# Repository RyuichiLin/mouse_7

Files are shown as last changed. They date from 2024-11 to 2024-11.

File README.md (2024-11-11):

# Micromouse: Mouse 7
This is a public repository for Team Kirbo's micromouse robot for IEEE of Long Island. 

This Micromouse project exists in its current state thanks to:

**Christopher Lobato**
- Implemented PID feedback loop control for the micromouse
- Troubleshooted micromouse firmware/hardware from the start of the project at Stony Brook University
- Helped transition from Arduino Nano to AT32UC3L0256 MCU using Microchip's SDK
- Troubleshooted micromouse firmware/hardware for Mouse 6 
- GOAT- countless hours of pure engineering passion and dedication

**Christopher Freeman**
- Implemented partial flood-fill algorithm from scratch starting mouse 6
- Troubleshooted micromouse firmware for Mouse 6
- GOAT- sharp, patient, and self-driven engineer

**Andy Zhuo**
- Designed a test board for alternatives to SHARP IR sensors to design a custom 3V3 IR sensor w/ similar characteristics to the SHARP sensors
- GOAT- underrated cheesecake enjoyer, can complete any task at hand

**Thomas Montchal**
- Initiated micromouse hardware design from the start of the project at Stony Brook University
- Designed 3D printed mounts for initial Mouse 4
- Helped design circuit for Mouse 4
- GOAT- competent and passionate electrical engineer, vast tinkering repertoire

**Rachel Leong**
- Implemented flood-fill algorithm for Mouse 4 at the start of the project at Stony Brook University 
- GOAT- a bright polymath and powerhouse of engineering

## Mouse 7 Active Team Members:
- Ryuichi Lin
  - Hardware design (schematic / PCB / component selection)
  - Embedded firmware development (drivers, wrappers for higher layers to utilize)
  - Initiate Python simulation effort
- Christopher Lobato
  - PID movement control development
  - Mouse movement development (acceleration/decceleration, diagonal movement via Python Simulation and w/ real hardware)
- Christopher Freeman
  - Mouse maze solving algorithm development (optimization via movement time calculation)
  - ESP32 Bluetooth serial module development (testing/verification before mouse integration)
- Andy Zhuo
  - SHARP IR sensor alternative development (schematic / PCB / component selection)
  - Command line interface development (debugging interface, data collection interface)

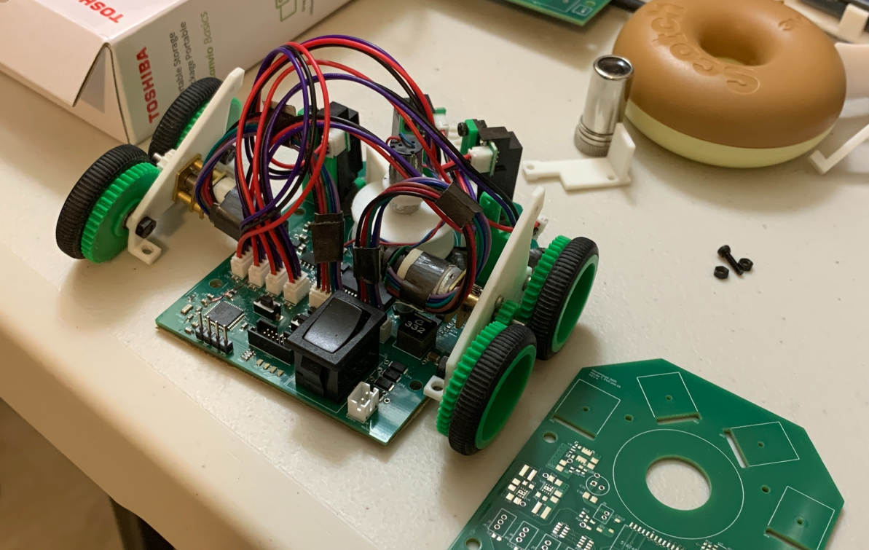
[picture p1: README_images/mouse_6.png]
Mouse 6 Image


This is the continuation of the micromouse journey- everything started in a lab with a handful of engineers and some Monster energy drinks.

## README Index
- [Repository Navigation](#repository-navigation)
- [Current Bot Overview](#current-bot-overview)
- [Work in Progress](#work-in-progress)
- [Version History](#version-history)

## Repository Navigation
- `HELP/`
  - Useful documentation for everyone:
  - Git guide
    - it's easy, and absolutely worth a quick read to use what Git provides at the bare minimum 
  - Doxygen Guide
    - important for standardizing C firmware format, and documentation generation
  - Sphinx Guide
    - important for standardizing Python software format, and documentation generation 
- `firmware/`
  - Firmware sourrce code:
    - AT32UC3L0256 MCU firmware
    - ESP32 Bluetooth module (work in progress)
- `hardware/`
  - 3D printed mount models
  - Mouse 7 hardware reference files:
    - Schematic PDF
    - PCB layout PDF
    - 3D model images
  - Bluetooth module hardware reference files:
    - Schematic PDF
    - PCB layout PDF
    - 3D model images
- `test_software/`
  - Python simulation test files

## Current Mouse Overview
- Below is a high level overview of the current micromouse and its features

### Firmware
- Mouse 7 runs on the AT32UC3L0256 MCU (32-bit AVR32 architecture MCU by Atmel/Microchip)
- Below is a block diagram outlining the firmware structure for (use Doxygen further documentation)

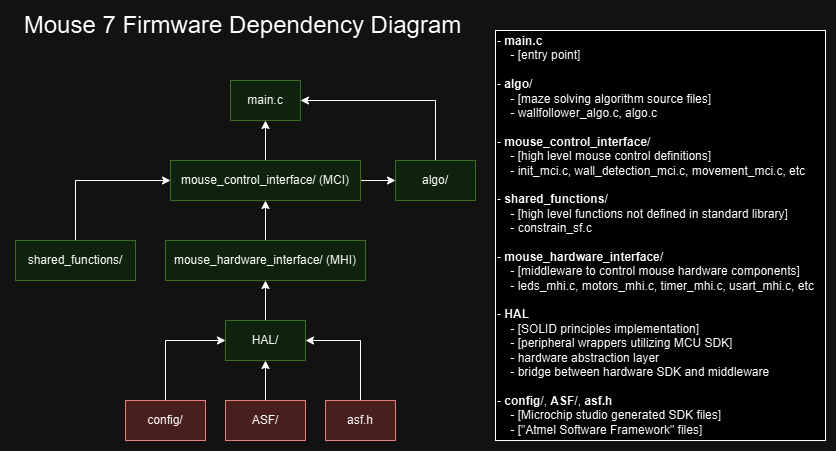
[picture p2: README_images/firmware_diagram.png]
Firmware Diagram

- Green items are written by us, red items are generated via Microchip Studio (hardware specific files)
- Mouse firmware structured to adhere to *SOLID Principles* (link: https://en.wikipedia.org/wiki/SOLID)
- Isolating hardware specific firmware under a **H**ardware **A**bstraction **L**ayer allows for easy plug and play when the time comes for a hardware upgrade or change

### Hardware
- Below is a block diagram outlining the main hardware components of Mouse 7:

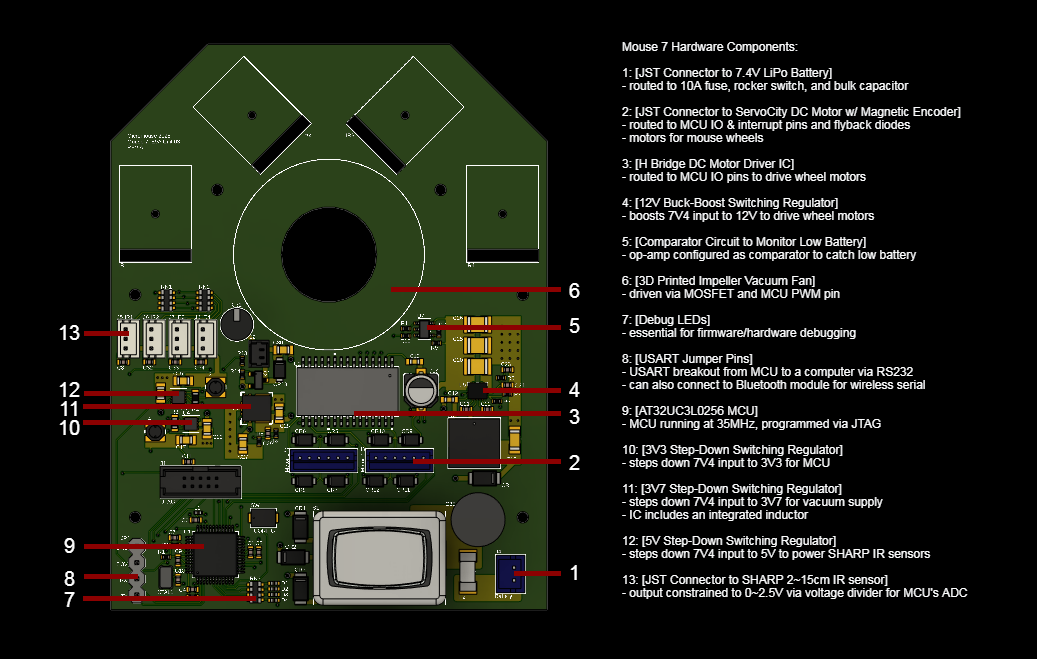
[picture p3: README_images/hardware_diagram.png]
Hardware Diagram

- Regarding the power supply circuitry, Texas Instruments has a fantastic tool to generate a circuit for whatever supply you need for your load: https://webench.ti.com/power-designer/
- Mouse 7's 3V3 and 5V circuits were found independent of the tool (Texas Instrument's regulator ICs have great documentation even without the webench tool), but the 12V and 3V7 supply circuits are webench generated, and work just fine

### Test Software
- Due to differences between the competetition maze and practice mazes, there is always a need to tune the mouse for the actual competition maze
- Python simulation software has been written to simulate hardware behavior to optimize mouse movement control and wall detection for any given maze
- Below is a block diagram outlining the test simulation structure (use Sphinx for further documentation)

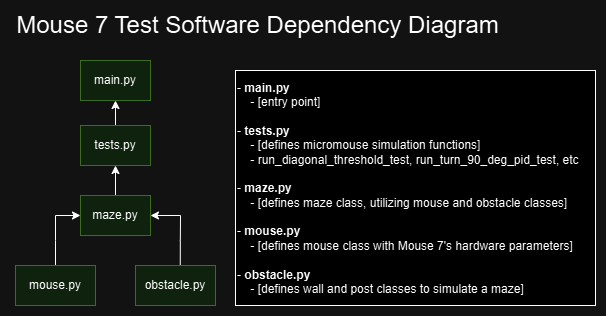
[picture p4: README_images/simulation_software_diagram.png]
Simulation Software Diagram


## Work in Progress
**Full SOLID principles implementation**
- mouse_hardware_interface layer incomplete- remove asf.h dependencies

**Python Simulation**
- simulate move forward PID (both one and two wall cases)

**Additional mouse movement options**
- diagonal movement, acceleration/decceleration, continuous movement

**Bluetooth module**
- verify functionality w/ custom made AT32UC3L0256 breakout board & Sparkfun ESP32 Bluetooth module board

**Serial command line interface**
- complete USART receive firmware for MCU 
- develop commands and appropriate responses to commands

**Maze algorithm updates**
- optimize mouse path for time taken for each type of movement (rotation, move forward, etc)

## Version History
### 1.0.0
- Initial revision
- Hardware is updated to mouse 7
- Firmware is outdated mouse 6 files
- New Python simulation files to avoid tuning mouse on the spot going forward

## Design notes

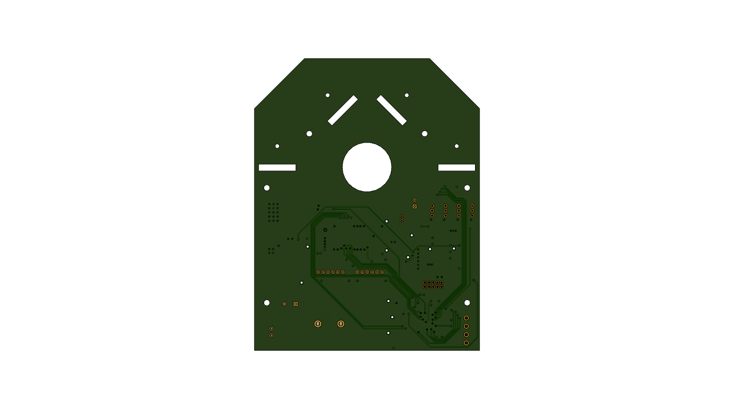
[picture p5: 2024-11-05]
hardware/mouse_7/3d_model/mouse_7_image_3.png

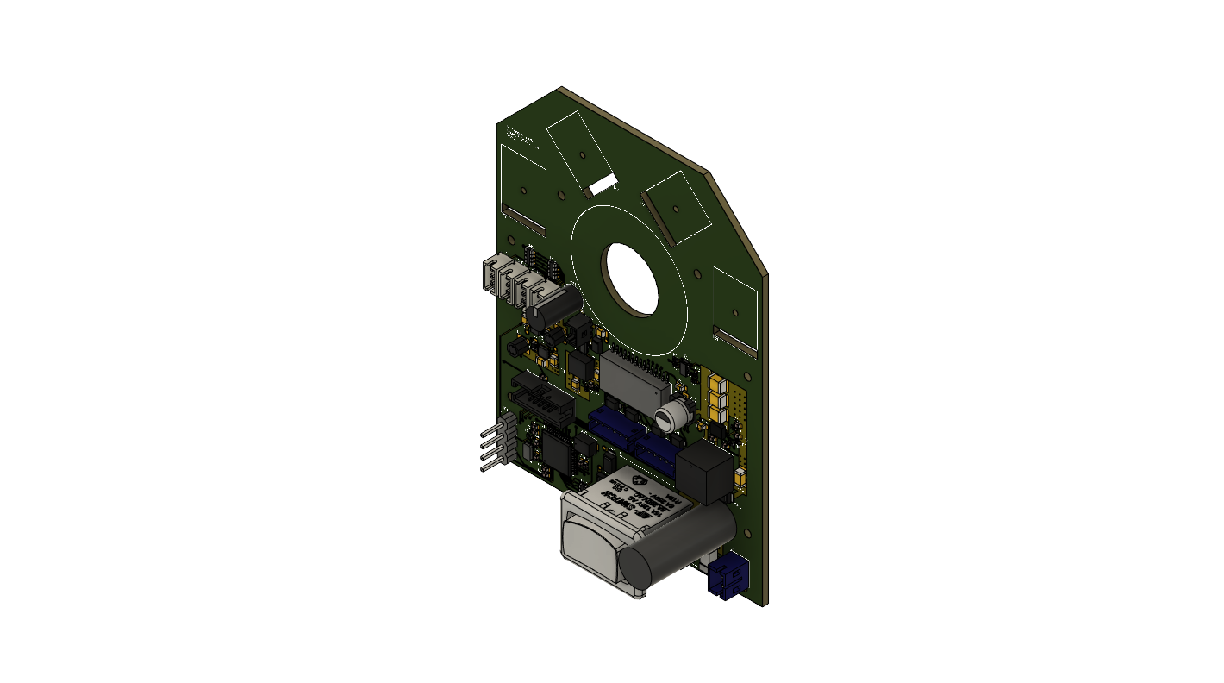
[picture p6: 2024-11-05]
hardware/mouse_7/3d_model/mouse_7_image_1.png

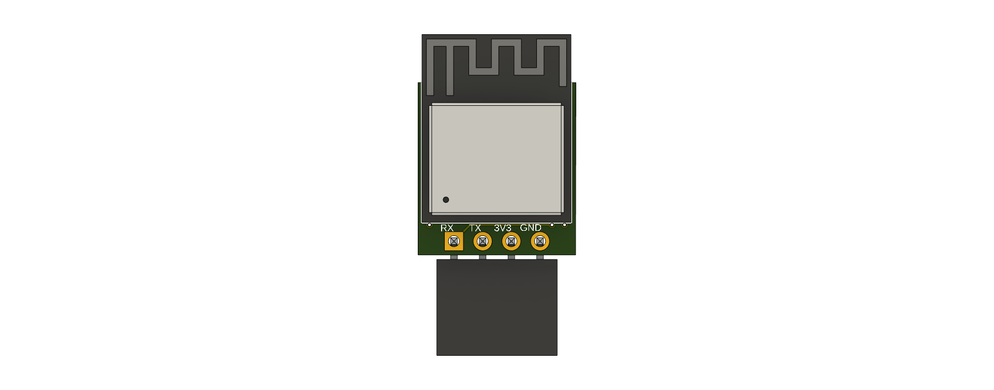
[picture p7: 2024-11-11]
hardware/bluetooth_module/3d_model/bluetooth_module_image_2.png

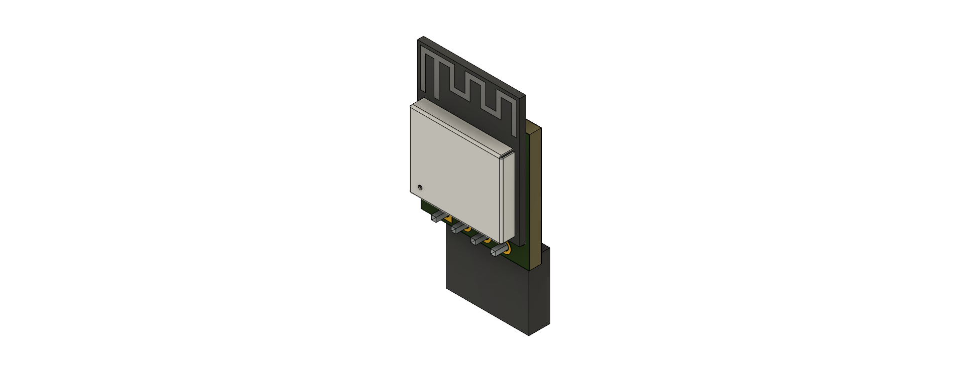
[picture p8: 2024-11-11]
hardware/bluetooth_module/3d_model/bluetooth_module_image_1.png

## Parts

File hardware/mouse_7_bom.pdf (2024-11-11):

Category | Vendor Item Number Item Description Quantity Per Package Cost Per Package Number of Packages Item Total Cost Part Link Symbol, Layout, & Designation on Mouse 7.0 Test Designation on Mouse 7.0 PCB 3D Model Link Comments
| - 7.4V LiPo battery, 900mAh, 46g, 30C - JST PH 2.0 pitch 2 position for power, 3 position for charging - 53mm x 16mm x 29mm (l x h x w)
| - JST PH 2.0 pitch 2 position pack both male and female TH - 50 male, 50 female

Power

Amazon | B096G4D6ZX URGENEX 7.4V Lipo Battery 2S 30C 900mAh Rechargeable Lipo Battery with PH2.0 Plug Compatible with Most 1/10, 1/16, 1/18, 1/24 Scale RC Cars Trucks 2 | $19.99 | 1 | $19.99 https://www.amazon.com/URGENEX-Battery-900mAh-Rechargeable-Campatibal/dp/B096G4D6ZX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
Amazon | B09DP9FZTX | CQRobot 50 Sets/200 Pieces 2.0 mm Pitch JST PH 2-Pin IC Sockets & Plugs Adapter Connector Male and Female Terminal, Crimp DIP Kit. for Industrial Integrated Circuit JST Connector Cable. 50 | $7.99 | 1 | $7.99 https://www.amazon.com/CQRobot-Connector-Terminal-Industrial-Integrated/dp/B09DP9FZTX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
Digikey | CMS04(TE12LQM)CT-ND DIODE SCHOTTKY 30V 5A M-FLAT 1 | $0.76 | 4 | $3.04 https://www.digikey.com/en/products/detail/toshiba-semiconductor-and-storage/CMS04-TE12L-Q-M/871534 https://app.ultralibrarian.com/details/873d4c59-1bbb-11ea-a124-0ad2c9526b44/Toshiba-Electronic-Devices-Storage-Corp-/CMS04-TE12L-Q-M-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
- schottky diode for everything except vacuum that needs 5A
- prevents up to 30V and allows 5A to pass
- for 3.3V, 5V, 12V, and 3.2V regulators
- small 370mV forward drop
Digikey | 296-53563-1-ND DC DC CONVERTER 1.2-6V | 1 | $3.48 | 1 | $3.48 https://www.digikey.com/en/products/detail/texas-instruments/TPSM84209RKHR/10273205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 https://app.ultralibrarian.com/details/72767a0a-9a13-11e9-ab3a-0a3560a4cccc/Texas-Instruments/TPSM84209RKHR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
- 3.7V 2A regulator for vacuum motor
- schematic generated w/ TI tool: HERE HERE
Digikey | 445-7665-1-ND CAP CER 22UF 10V X5R 0805 1 | $0.39 | 2 | $0.78 https://www.digikey.com/en/products/detail/tdk-corporation/C2012X5R1A226M125AB/2733100 n/a
- Cin for vacuum fan regulator circuit
- 0805 package
- 22uF
Digikey | 445-8239-1-ND CAP CER 47UF 10V X5R 0805 1 | $0.79 | 3 | $2.37 https://www.digikey.com/en/products/detail/tdk-corporation/C2012X5R1A476M125AC/2812455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 n/a
- Cout for vacuum fan regulator circuit
- 0805 package
- 47uF
Digikey | 399-C0402C331J5JAC7867CT-ND CAP CER 330PF 50V U2J 0402 1 | $0.24 | 1 | $0.24 https://www.digikey.com/en/products/detail/kemet/C0402C331J5JAC7867/6176500 n/a
- Cff for vacuum fan regulator circuit
- 0402 package
- 330pF
Digikey | 541-10.0KLCT-NDRES SMD 10K OHM 1% 1/16W 0402 1 | $0.10 | 1 | $0.10 https://www.digikey.com/en/products/detail/vishay-dale/CRCW040210K0FKED/1178121 n/a
- Rfbt for vacuum fan regulator circuit
- 0402 package
- 10k Ohm resistor
Digikey | 541-1.91KLCT-NDRES SMD 1.91K OHM 1% 1/16W 0402 1 | $0.10 | 1 | $0.10 https://www.digikey.com/en/products/detail/vishay-dale/CRCW04021K91FKED/1178037 n/a
- Rfbb for vacuum fan regulator circuit
- 0402 package
- 1.91k Ohm resistor
Digikey | 296-TPS61288RQQRCT-ND IC REG BOOST ADJ 15A 11VQFN1 | $5.89 | 1 | $5.89 https://www.digikey.com/en/products/detail/texas-instruments/TPS61288RQQR/13627146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 https://app.ultralibrarian.com/details/b8fe61ee-f9ad-11ea-b55a-0a34d6323d74/Texas-Instruments/TPS61288RQQR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
- 12V 3A regulator for wheel motor driver
- schematic generated w/ TI tool: https://webench.ti.com/appinfo/webench/scripts/SDP.cgi?ID=AA12043C39DD7B4B
Digikey | 445-4042-1-ND CAP CER 10UF 16V X7R 1206 1 | $0.30 | 1 | $0.30 https://www.digikey.com/en/products/detail/tdk-corporation/C3216X7R1C106K160AC/1965630 n/a
- Cin for wheel motor regulator circuit
- 1206 package
- 10uF
Digikey | 445-1314-1-ND CAP CER 0.1UF 50V X7R 0603 1 | $0.10 | 1 | $0.10 https://www.digikey.com/en/products/detail/tdk-corporation/C1608X7R1H104K080AA/513811 n/a
- Cinx for wheel motor regulator circuit
- 0603 package
- 0.1uF
Coilcraft | XAL7070-332 | XAL7070-332MEC | 1 | $3.25 | 1 | $3.25 https://www.coilcraft.com/en-us/products/power/shielded-inductors/molded-inductor/xal/xal7070/xal7070-332/ https://app.ultralibrarian.com/details/c70f84e9-0c17-11ee-9288-0ae0a3b49db5/Coilcraft/XAL7070-332MEC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 - L1 for wheel motor regulator circuit
Digikey | 445-4952-1-ND CAP CER 0.1UF 16V X7R 0402 1 | $0.10 | 1 | $0.10 https://www.digikey.com/en/products/detail/tdk-corporation/C1005X7R1C104K050BC/2093220 n/a
- Cbst for wheel motor regulator circuit
- 0402 package
- 0.1uF
Digikey | 445-9097-1-ND CAP CER 2.2UF 10V X7S 0402 1 | $0.29 | 1 | $0.29 https://www.digikey.com/en/products/detail/tdk-corporation/C1005X7S1A225K050BC/3661557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 n/a
- Cvcc for wheel motor regulator circuit
- 0402 package
- 2.2uF
Digikey | 541-34.0KLCT-NDRES SMD 34K OHM 1% 1/16W 0402 1 | $0.10 | 1 | $0.10 https://www.digikey.com/en/products/detail/vishay-dale/CRCW040234K0FKED/1178180 n/a
- Rcomp for wheel motor regulator circuit
- 0402 package
- 34k Ohms
Digikey | 490-16432-1-ND CAP CER 0.039UF 16V X7R 04021 | $0.10 | 1 | $0.10 https://www.digikey.com/en/products/detail/murata-electronics/GCM155R71C393KA37D/7363176 n/a
- Ccomp for wheel motor regulator circuit
- 0402 package
- 39nF
Digikey | 399-11256-1-ND CAP CER 82PF 25V C0G/NP0 0402 1 | $0.49 | 1 | $0.49 https://www.digikey.com/en/products/detail/kemet/CBR04C820F3GAC/4377017 n/a
- Ccomp2 for wheel motor regulator circuit
- 0402 package
- 82pF
Digikey | 541-931KLCT-NDRES SMD 931K OHM 1% 1/16W 0402 1 | $0.10 | 1 | $0.10 https://www.digikey.com/en/products/detail/vishay-dale/CRCW0402931KFKED/1178346 n/a
- Rfbt for wheel motor regulator circuit
- 0402 package
- 931k Ohms
Digikey | 541-48.7KLCT-NDRES SMD 48.7K OHM 1% 1/16W 0402 1 | $0.10 | 1 | $0.10 https://www.digikey.com/en/products/detail/vishay-dale/CRCW040248K7FKED/1178199 n/a
- Rfbb for wheel motor regulator circuit
- 0402 package
- 48.7k Ohms
Digikey | 490-16309-1-ND CAP CER 47UF 16V X6S 1210 1 | $0.52 | 3 | $1.56 https://www.digikey.com/en/products/detail/murata-electronics/GRM32EC81C476KE15K/7363053 n/a
- Cout for wheel motor regulator circuit
- 1210 package
- 47uF
Digikey | EG5554-ND | SWITCH ROCKER SPST 15A 125V 1 | $1.64 | 1 | $1.64 https://www.digikey.com/en/products/detail/e-switch/R1966ABLKBLKEP/1805067 - https://www.mouser.com/ProductDetail/E-Switch/R1966ABLKBLKEP?qs=fwxlpxwtDRcZsx8M4AZ8tA%3D%3D
- switch for on/off of entire mouse
- rated for 15A (AC), can hopefully handle 9A DC
Digikey | 283-5179-1-ND FUSE BRD MNT 10A 125VAC/VDC 2SMD 1 | $0.91 | 1 | $0.91 https://www.digikey.com/en/products/detail/eaton-electronics-division/CB61F10A-TR2/3526138 https://www.mouser.com/ProductDetail/Bussmann-Eaton/CB61F10A-TR2?qs=3W28jC%252BmlM2sYw8RFxQ%2Faw%3D%3D
- 10A fuse for entire mouse
- 3A for wheels + 2A for vacuum + 1A for 3.3V + 1A for 5V = 7A | Extra new
Digikey | P122314CT-ND CAP ALUM 1200UF 20% 16V RADIAL 1 | $0.49 | 1 | $0.49 https://www.digikey.com/en/products/detail/panasonic-electronic-components/EEU-FS1C122LB/7381180 https://www.mouser.com/ProductDetail/Panasonic/EEU-FS1C122LB?qs=gt1LBUVyoHmQ1%252BC95E8BAw%3D%3D - 1.2mF 16V bulk cap for entire mouse | Extra new
Digikey | 296-39450-1-ND IC REG BUCK 5V 500MA 8WSON1 | $1.36 | 1 | $1.36 https://www.digikey.com/en/products/detail/texas-instruments/TPS62173DSGR/2833458 https://app.ultralibrarian.com/details/16ac426d-103f-11e9-ab3a-0a3560a4cccc/Texas-Instruments/TPS62173DSGR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
- 5V, 500mA switching regulator
- used to power Sharp sensors
Digikey | 296-39449-1-ND IC REG BUCK 3.3V 500MA 8WSON 1 | $1.36 | 1 | $1.36 https://www.digikey.com/en/products/detail/texas-instruments/TPS62172DSGR/2833456 https://app.ultralibrarian.com/details/16ac3ea9-103f-11e9-ab3a-0a3560a4cccc/Texas-Instruments/TPS62172DSGR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
- 3.3V, 500mA switching regulator
- used to power MCU
Digikey | 445-6857-1-ND CAP CER 10UF 10V X7R 0805 1 | $0.31 | 2 | $0.62 https://www.digikey.com/en/products/detail/tdk-corporation/C2012X7R1A106K125AC/2619198 n/a
- 10uF ceramic cap needed for 5V and 3.3V switching regulator
- between VIN and PGND (pg 21 pdf of datasheet)
- 0805 package

Category | Vendor | Item Number

Item Description

Quantity Per Package

Cost Per Package

Number of Packages | Item Total Cost | Part Link

Symbol, Layout, &
3D Model Link | Comments

Designation on Mouse 7.0 Test

Designation on Mouse 7.0 PCB

Digikey | 445-7665-1-ND CAP CER 22UF 10V X5R 0805 1 | $0.39 | 2 | $0.78 https://www.digikey.com/en/products/detail/tdk-corporation/C2012X5R1A226M125AB/2733100 n/a
- 22uF ceramic cap needed for 5V and 3.3V switching regulator
- between SW and FB (pg 21 pdf of datasheet)
Digikey | 541-100KHCT-NDRES SMD 100K OHM 1% 1/10W 0603 1 | $0.10 | 2 | $0.20 https://www.digikey.com/en/products/detail/vishay-dale/CRCW0603100KFKEA/1174896 n/a
- 100k Ohm resistor needed for 5V and 3.3V switching regulator
- between SW/VOS and PG (pg 21 pdf of datasheet)
- smaller 0603 package
Digikey | 732-2613-1-ND FIXED IND 2.2UH 1.8A 66 MOHM SMD 1 | $1.64 | 2 | $3.28 https://www.digikey.com/en/products/detail/w%C3%BCrth-elektronik/744025002/2445620 https://www.mouser.com/ProductDetail/Wurth-Elektronik/744025002?qs=rS3zZhy2AQOJdJOD4WhGug%3D%3D
- 2.2uH inductor needed for 5V and 3.3V switching regulator
- between SW and 100k Ohm resistor (pg 21 pdf of datasheet) | (NEW, old dupe)
Digikey | 296-TLV9301IDBVRCT-ND IC OPAMP GP 1 CIRCUIT SOT23-5 1 | $0.58 | 1 | $0.58 https://www.digikey.com/en/products/detail/texas-instruments/TLV9301IDBVR/12165123 https://app.ultralibrarian.com/details/268976cb-c80b-11e9-ab3a-0a3560a4cccc/Texas-Instruments/TLV9301IDBVR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
- low battery voltage indicator op amp
- to be used as comparator to turn on/off regulators
Digikey | P118KLCT-ND | RES SMD 118K OHM 1% 1/10W 0402 1 | $0.10 | 1 | $0.10 https://www.digikey.com/en/products/detail/panasonic-electronic-components/ERJ-2RKF1183X/192103 n/a
- R2 for low battery voltage comparator circuit
- 0402 package
- 118k Ohms
Digikey | 541-100KLCT-NDRES SMD 100K OHM 1% 1/16W 0402 1 | $0.10 | 1 | $0.10 https://www.digikey.com/en/products/detail/vishay-dale/CRCW0402100KFKED/1178235 n/a
- R1 for low battery voltage comparator circuit
- 0402 package
- 100k Ohms
Digikey | 541-10.0KLCT-NDRES SMD 10K OHM 1% 1/16W 0402 1 | $0.10 | 1 | $0.10 https://www.digikey.com/en/products/detail/vishay-dale/CRCW040210K0FKED/1178121 n/a
- R1 for comparator output divider
- 0402 package
- 10k ohms | (NEW, dupe)
Digikey | P3.74KLCT-ND RES SMD 3.74K OHM 1% 1/10W 0402 1 | $0.10 | 1 | $0.10 https://www.digikey.com/en/products/detail/panasonic-electronic-components/ERJ-2RKF3741X/192286 n/a
- R2 for comparator output divider
- 0402 package
- 3.74k ohms | NEW

Wheel Motor Related

Digikey | TB6561FG8ELCT-ND IC MOTOR DRIVER 10V-36V 30SSOP 1 | $3.51 | 1 | $3.51 https://www.digikey.com/en/products/detail/toshiba-semiconductor-and-storage/TB6561FG-8-EL/1730056 https://app.ultralibrarian.com/details/84a3ee1c-5a2c-11eb-9033-0a34d6323d74/Toshiba-Electronic-Devices-Storage-Corp-/TB6561FG-8-EL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
- H bridge PWM interface brushed motor driver
- 10-36V supply, 3A output max, 30-BSOP
Digikey | 445-7456-1-ND CAP CER 0.1UF 50V X5R 0603 1 | $0.11 | 1 | $0.11 https://www.digikey.com/en/products/detail/tdk-corporation/C1608X5R1H104K080AA/2732891 n/a
- C2 0.1uF cap for 5V output from motor driver
- datasheet pg 8: HERE
- 0603 package
Digikey | P121394CT-ND CAP ALUM HYB 47UF 20% 25V SMD 1 | $1.45 | 1 | $1.45 https://www.digikey.com/en/products/detail/panasonic-electronic-components/EEH-ZK1E470R/6564642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 https://www.mouser.com/ProductDetail/Panasonic/EEH-ZK1E470R?qs=FNcb6ahWXRxnLCe3Ulph5A%3D%3D
- C1 47uF polymer cap for motor driver supply
- datasheet pg 8
Servocity | 638103 Gear Motor with Encoder | 1 | $19.99 | 2 | $39.98 https://www.servocity.com/4900-rpm-micro-gear-motor-w-encoder/
- Gear motors, 4900rpm w/ encoders
- 6 position 1.5 pitch ZH JST
Pololu | 1087 Black plastic wheels with silicone tires 2 | $4.95 | 1 | $4.95 https://www.pololu.com/product/1087
- Wheels, 32mm diameter, 3mm D output shaft
- we'll use just the rubber tire and make a custom wheel
Amazon | B09NCCXPGM CQRobot 100 Sets/800 Pieces 1.5 mm Pitch JST ZH 6-Pin IC Sockets & Plugs Adapter Connector Male and Female Terminal, Crimp DIP Kit. for Industrial Integrated Circuit JST Connector Cable. 100 | $9.58 | 1 | $9.58 https://www.amazon.com/CQRobot-Connector-Terminal-Industrial-Integrated/dp/B09NCCXPGM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

https://www.jst-mfg.com/product/index.php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 - JST ZH 6 position male (receptacle) TH connector
Amazon | B07FW18RQY | uxcell 683ZZ Ball Bearing 3mm x 7mm x 3mm Double Shielded Deep Groove Bearings, Carbon Steel 20pcs 20 | $7.99 | 1 | $7.99 https://www.amazon.com/uxcell-Bearing-Double-Shielded-Bearings/dp/B07FW18RQY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 - 3mm ball bearings to be embedde into custom wheels
Servocity | 1500-0010-0003 1500 Series Plastic Spacer (3mm ID x 5mm OD, 1mm Thickness) - 12 Pack 12 | $1.87 | 1 | $1.87 https://www.servocity.com/1500-series-plastic-spacer-3mm-id-x-5mm-od-1mm-thickness-12-pack/ - 3mm plastic spacers to put between wheel and mount
Amazon | B0BKRQSMFL FOLIV 700PCS M3 x 5/6/8/10/12/14/16/18/20/25/30mm Button Hex Head Cap Screws M3 Metric Machine Screws Bolts Nuts Washer Assortment Kit, 10.9 Grade Alloy Steel 10-50 | $15.29 | 1 | $15.29 https://www.amazon.com/gp/product/B0BKRQSMFL/ref=ox_sc_act_title_1?smid=A3ILXS83DKRO8O&th=1 - M3 button head screws to serve as wheel axels
Digikey | 1727-7806-1-ND DIODE SCHOTTKY 60V 3A SOD123W 1 | $0.39 | 8 | $3.12 https://www.digikey.com/en/products/detail/nexperia-usa-inc/PMEG60T30ELRX/9086223 https://app.ultralibrarian.com/details/785255d6-6dbf-11ee-9288-0ae0a3b49db5/Nexperia/PMEG60T30ELRX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 - Flyback diodes for EMF protection

Vacuum Fan Related

Amazon | B08RMQP6YP 1.25mm Male and Female Connectors Socket and Plug with Pre-Crimped Cables Compatible with JST Molex PicoBlade 1.25 for Pixhawk Silicone 13cm Wire (Male and Female) 20 | $18.99 | 1 | $18.99 https://www.amazon.com/Connectors-Pre-Crimped-Compatible-PicoBlade-Silicone/dp/B08RMQP6YP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 n/a
- Molex picoblade connector various positions,
- includes 3 position 1.25mm pitch male and female connector, 20 of each
- includes 10cm precrimped wire
- to be used to extend HGLRC wire
Digikey | DMN3200U-7DICT-ND MOSFET N-CH 30V 2.2A SOT23-31 | $0.45 | 1 | $0.45 https://www.digikey.com/en/products/detail/diodes-incorporated/DMN3200U-7/1778821 https://www.mouser.com/ProductDetail/Diodes-Incorporated/DMN3200U-7?qs=oDfC%252BbpzniwrIf3%2FMV01IQ%3D%3D - 2.2A 30V MOSFET to switch on/off regulator power to vacuum fan | NEW
Digikey | P17216CT-ND | RES 47 OHM 1% 1/4W 0402 | 1 | $0.23 | 1 | $0.23 https://www.digikey.com/en/products/detail/panasonic-electronic-components/ERJ-PA2F47R0X/5402642 n/a | - 47 Ohm gate resistor for MOSFET to limit surge curernt | NEW
Digikey | 541-10.0KLCT-NDRES SMD 10K OHM 1% 1/16W 0402 1 | $0.10 | 1 | $0.10 https://www.digikey.com/en/products/detail/vishay-dale/CRCW040210K0FKED/1178121 n/a
- 10k Ohm resistor for pulling down input to MOSFET to ensure low
| | | | | | | - 0402 package | (NEW, dupe)
Digikey | 493-3813-1-ND RNE1C101MDS1PX | 1 | $0.76 | 1 | $0.76 https://www.digikey.com/en/products/detail/nichicon/RNE1C101MDS1PX/2239221 https://app.ultralibrarian.com/details/8611d1e7-1076-11e9-ab3a-0a3560a4cccc/Nichicon/RNE1C101MDS1PX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 100uF capacitor for vacuum fan driver
Digikey | 4988-NMC0805X7R104K50TRPFCT-ND CAP SMT08050.1F50VDC | 1 | $0.24 | 1 | $0.24 https://www.digikey.com/en/products/detail/nic-components-corp/NMC0805X7R104K50TRPF/18895932 n/a
- 0.1uF cap for brushless motor driver
- 0805 package
Amazon | B07CFQMF1M 8pcs 8520 Motor 8.5x20mm 15000KV Brushed Motors 4CW 4CCW Coreless Motor with JST-1.25 Connector for D JI Ryze Tello 720P Camera WiFi FPV RC Quadcopter M80S E013 Plus Tiny 8X Frame Kit etc 8 | $18.99 | 1 | $18.99 https://www.amazon.com/8-5x20mm-15000KV-Coreless-JST-1-25-Connector/dp/B07CFQMF1M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 n/a
- 15000KV brushed DC motor for vacuum fan
- 2p 1.25mm pitch picoblade connector
Digikey | WM1731-ND | CONN HEADER VERT 2POS 1.25MM 1 | $0.23 | 1 | $0.23 https://www.digikey.com/en/products/detail/molex/0530470210/242853?s=N4IgTCBcDaIKwGYAMAWA7EsBGJIC6AvkA
- https://app.ultralibrarian.com/details/56453440-d29f-11ea-b5d0-0aebb021a1ea/Molex-Connector-Corporation/530470210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
- https://www.molex.com/en-us/products/part-detail/530470210
- motor to board connector for vacuum fan
- 2p 1.25mm pitch picoblade connector
Digikey | 1727-7806-1-ND DIODE SCHOTTKY 60V 3A SOD123W 1 | $0.39 | 2 | $0.78 https://www.digikey.com/en/products/detail/nexperia-usa-inc/PMEG60T30ELRX/9086223 https://app.ultralibrarian.com/details/785255d6-6dbf-11ee-9288-0ae0a3b49db5/Nexperia/PMEG60T30ELRX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 - Flyback diodes for EMF protection

Ball Caster,
nuts, screws
Amazon | B0BTYDZVM8 | 1 Oz (23 Grams) 3000-CPS Super Glue All Purpose with Anti Clog Cap. Ca Glue - Adhesive SuperGlue. Cyanoacrylate Glue for Hard Plastics, DIY Craft, Metal and Many More 1 | $6.99 | 1 | $6.99 https://www.amazon.com/gp/product/B0BTYDZVM8/ref=sw_img_1?smid=A3O523LQQ2NT7Z&th=1 - superglue to attach 3D printed mounts to PCB

Category | Vendor | Item Number

Item Description

Quantity Per Package

Cost Per Package

Number of Packages | Item Total Cost | Part Link

Symbol, Layout, &
3D Model Link | Comments

Designation on Mouse 7.0 Test

Designation on Mouse 7.0 PCB

IR Sensing

Digikey | 1855-1027-ND | SENSOR OPTICAL 2-15CM ANALOG 1 | $8.45 | 4 | $33.80 https://www.digikey.com/en/products/detail/sharp-socle-technology/GP2Y0A51SK0F/4103863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 https://www.mouser.com/ProductDetail/Sharp-Microelectronics/GP2Y0A51SK0F?qs=Qrpqs4v%252BmsahSKJyPt06pw%3D%3D
- Sharp IR distance sensor 2-15cm
- shortest range sharp IR sensor available
- connects w/ 3 position ZH JST connector
- needs 10uF cap
Amazon | B09NC8Y2PK | CQRobot 100 Sets/500 Pieces 1.5 mm Pitch JST ZH 3-Pin IC Sockets & Plugs Adapter Connector Male and Female Terminal, Crimp DIP Kit. for Industrial Integrated Circuit JST Connector Cable. 50 | $11.99 | 1 | $11.99 https://www.amazon.com/CQRobot-Connector-Terminal-Industrial-Integrated/dp/B09NC8Y2PK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 https://www.jst-mfg.com/product/index.php?series=290
- JST ZH 1.5 pitch 3 position pack both male and female TH
- 50 male, 50 female
Digikey | 490-GRM155R61A106ME11DCT-ND CAP CER 10UF 10V X5R 0402 1 | $0.13 | 4 | $0.52 https://www.digikey.com/en/products/detail/murata-electronics/GRM155R61A106ME11D/12091056 n/a
- 10uF ceramic capacitor, SMD 0402
- needed for Sharp IR sensors | NEW
Digikey | CAY16-1001F4LFCT-ND RES ARRAY 4 RES 1K OHM 12061 | $0.10 | 1 | $0.10 https://www.digikey.com/en/products/detail/bourns-inc/CAY16-1001F4LF/2566504 https://app.ultralibrarian.com/details/ccdadb33-1071-11e9-ab3a-0a3560a4cccc/Bourns-Electronics/CAY16-1001F4LF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
- R1 resistor array to drop 2.5V max from IR sensor output to 1.8V
- 1k Ohm resistor array, 4 resistors
Digikey | CAY16-2201F4LFCT-ND RES ARRAY 4 RES 2.2K OHM 1206 1 | $0.10 | 1 | $0.10 https://www.digikey.com/en/products/detail/bourns-inc/CAY16-2201F4LF/2566534 https://app.ultralibrarian.com/details/1c159e3e-f9f4-11ed-b159-0a34d6323d74/Bourns-Electronics/CAY16-2201F4LF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
- R2 resistor to drop 2.5V max from IR sensor output to 1.8V
- 2.2k Ohms calculated w/ voltage divider equation
- resistor array, 4 resistors

MCU

Digikey | 1175-1733-ND | CONN HEADER VERT 10POS 1.27MM 1 | $0.68 | 1 | $0.68 https://www.digikey.com/en/products/detail/cnc-tech/3221-10-0100-00/4878932 https://www.arrow.com/en/products/3221-10-0100-00/cnc-tech-llc
- 2x5 TH JTAG programming header
- small 1.27 pitch w/ key slot and shroud
Digikey | 2151-RT3215-32.768-12.5-TR-10PPMCT-ND CRYSTAL 32.7680KHZ 12.5PF SMD 1 | $0.42 | 1 | $0.42 https://www.digikey.com/en/products/detail/raltron-electronics/RT3215-32-768-12-5-TR-10PPM/13151073 https://app.ultralibrarian.com/details/ce5d9187-838b-11ec-9033-0a34d6323d74/Raltron/RT3215-32-768-12-5-TR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 - 32.768kHz external crystal
Digikey | 490-GQM1555C2D220FB01DCT-ND CAP CER 22PF 200V NP0 04021 | $0.61 | 2 | $1.22 https://www.digikey.com/en/products/detail/murata-electronics/GQM1555C2D220FB01D/5882005 https://app.ultralibrarian.com/details/d28e9410-f5b2-11eb-9033-0a34d6323d74/Murata/GQM1555C2D3R5CB01J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
- 22pF caps for external crystal
- needed on each crystal terminal
- 0402 package | NEW
Amazon | B07BJJC3R6 | NOYITO TTL to RS232 Module TTL RS232 Male Female Mutual Conversion Module Serial Level Conversion to SP232 TTL Serial Port Communicates with RS232 Level Device 15KV ESD Protect (Female) 1 | $7.99 | 1 | $7.99 https://www.amazon.com/NOYITO-Module-Conversion-Arduino-communicates/dp/B07BJJC3R6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 not needed | - TTL to DB-9 (DE-9) translator for serial out
Amazon | B0759HSLP1 | OIKWAN USB to RS232, USB Serial Adapter with FTDI Chipset,USB 2.0 to Male DB9 Serial Cable for Windows 11,10, 8, 7, Vista, XP, 2000, Linux and Mac OS(6ft)… 1 | $11.99 | 1 | $11.99 https://www.amazon.com/Adapter-Chipset%EF%BC%8CDB9-Serial-Converter-Windows/dp/B0759HSLP1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 not needed | - DB-9 (DE-9) to USB A for serial out
Digikey | AT32UC3L0256-AUT-ND IC MCU 32BIT 256KB FLASH 48TQFP 1 | $10.19 | 1 | $10.19 https://www.digikey.com/en/products/detail/microchip-technology/AT32UC3L0256-AUT/3046397 https://app.ultralibrarian.com/details/89115949-109b-11e9-ab3a-0a3560a4cccc/Microchip/AT32UC3L0256-AUT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
- AT32UC3L0256 AVR MCU to replace Arduino
- 50MHz, faster than controller above, operates on 3.3V
- 12b ADC, PWM, programmed via JTAG and aWire
- schematic checklist: HERE
Digikey | 490-GRM155R61A106ME11DCT-ND CAP CER 10UF 10V X5R 0402 1 | $0.13 | 1 | $0.13 https://www.digikey.com/en/products/detail/murata-electronics/GRM155R61A106ME11D/12091056 n/a
- 10uF capacitor for AT32UC3L0256 VDDin
- page 4 of schematic checklist
- small 0402 package | NEW
Digikey | 445-4952-1-ND CAP CER 0.1UF 16V X7R 0402 1 | $0.10 | 3 | $0.30 https://www.digikey.com/en/products/detail/tdk-corporation/C1005X7R1C104K050BC/2093220 n/a
- 0.1uf ceramic cap for AT32UC3L0256 VDDin, VDDio, and VDDcore
- page 4 of schematic checklist
- 0402 package | (NEW, dupe)
Digikey | 445-9097-1-ND CAP CER 2.2UF 10V X7S 0402 1 | $0.29 | 1 | $0.29 https://www.digikey.com/en/products/detail/tdk-corporation/C1005X7S1A225K050BC/3661557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 n/a
- 2.2uF ceramic cap for AT32UC3L0256 VDDio, and VDDcore
- page 4 of schematic checklist
- 0402 package | (NEW, dupe)
Digikey | 445-4952-1-ND CAP CER 0.1UF 16V X7R 0402 1 | $0.10 | 1 | $0.10 https://www.digikey.com/en/products/detail/tdk-corporation/C1005X7R1C104K050BC/2093220 n/a
- 0.1uF ceramic cap for AT32UC3L0256 VDDana and ADVREF
- page 5 of schematic checklist
- 0402 package | (NEW, dupe)
Digikey | 732-74269241152CT-ND WETMSB SMT EMI SUPPRESSION FERR 1 | $0.13 | 1 | $0.13 https://www.digikey.com/en/products/detail/w%C3%BCrth-elektronik/74269241152/17830009 https://app.ultralibrarian.com/details/ab67cd4b-c364-11ed-b159-0a34d6323d74/Wurth-Electronics/74269244182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
- ferrite bead for for AT32UC3L0256 VDDana and ADVREF
- page 5 of schematic checklist, and page 15 on xplained dev board schematic: HERE
- 0402 package | NEW
Digikey | 445-4952-1-ND CAP CER 0.1UF 16V X7R 0402 1 | $0.10 | 1 | $0.10 https://www.digikey.com/en/products/detail/tdk-corporation/C1005X7R1C104K050BC/2093220 n/a
- 0.1uF ceramic cap for JTAG on AT32UC3L0256
- 0402 package | (NEW, dupe)
Digikey | 541-10.0KLCT-NDRES SMD 10K OHM 1% 1/16W 0402 1 | $0.10 | 1 | $0.10 https://www.digikey.com/en/products/detail/vishay-dale/CRCW040210K0FKED/1178121 n/a
- 10k resistor for pulling down enable signal
- 0402 package | (NEW, dupe)

Bluetooth

Digikey | 1965-ESP32-PICO-MINI-02-N8R2CT-ND RF TXRX MOD BT WIFI THCHAS MNT 1 | $3.50 | 1 | $3.50 https://www.digikey.com/en/products/detail/espressif-systems/ESP32-PICO-MINI-02-N8R2/14317715

https://www.mouser.com/ProductDetail/Espressif-Systems/ESP32-PICO-MINI-02-N8R2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

- ESP32 bluetooth module to serve as a serial bridge between mouse and laptop
- perfect for our application- Sparkfun has a dev board doing exactly what we want | Extra Extra new
Digikey | 445-9077-1-ND CAP CER 22UF 10V X5R 0603 1 | $0.34 | 1 | $0.34 https://www.digikey.com/en/products/detail/tdk-corporation/C1608X5R1A226M080AC/3661560 n/a
- 22uF cap to decouple ESP32 module power
- 0603 package | Extra Extra new
Digikey | 445-4952-1-ND CAP CER 0.1UF 16V X7R 0402 1 | $0.10 | 1 | $0.10 https://www.digikey.com/en/products/detail/tdk-corporation/C1005X7R1C104K050BC/2093220 n/a
- 0.1uF cap to decouple ESP32 module power
- 0402 package | (NEW, dupe)
Digikey | 541-10.0KLCT-NDRES SMD 10K OHM 1% 1/16W 0402 1 | $0.10 | 1 | $0.10 https://www.digikey.com/en/products/detail/vishay-dale/CRCW040210K0FKED/1178121 n/a
- 10k resistor to slow down ESP32 module power up
- 0402 package | (NEW, dupe)
Digikey | 445-9086-1-ND CAP CER 1UF 16V X6S 0402 | 1 | $0.10 | 1 | $0.10 https://www.digikey.com/en/products/detail/tdk-corporation/C1005X6S1C105K050BC/3661565 n/a
- 1uF cap to slow down ESP32 module power up
- 0402 package | Extra Extra new
Digikey | 2449-CS1213AGF160CT-ND SWITCH TACTILE SPST-NO 0.05A 50V 1 | $0.40 | 1 | $0.40 https://www.digikey.com/en/products/detail/cit-relay-and-switch/CS1213AGF160/16607723 https://app.ultralibrarian.com/details/600608b2-d687-11ed-b159-0a34d6323d74/CIT-Relay-Switch/CS1213AGF260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 - pushbutton for ESP32 module boot option | (NEW, dupe)
Digikey | PPPC041LGBN-RCCONN HDR 4POS 0.1 GOLD PCB R/A 1 | $0.68 | 1 | $0.68 https://www.digikey.com/en/products/detail/sullins-connector-solutions/PPPC041LGBN-RC/775937 https://octopart.com/pppc041lgbn-rc-sullins-270383 - female 2.54mm pitch connector to connect to mouse | Extra Extra new

Misc

Digikey | 2449-CS1213AGF160CT-ND SWITCH TACTILE SPST-NO 0.05A 50V 1 | $0.40 | 1 | $0.40 https://www.digikey.com/en/products/detail/cit-relay-and-switch/CS1213AGF160/16607723 https://app.ultralibrarian.com/details/600608b2-d687-11ed-b159-0a34d6323d74/CIT-Relay-Switch/CS1213AGF260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
- 3.9mm x 2.9mm smd pushbutton for config
- 2mm high | NEW | Extra new
Digikey | 754-1105-1-ND LED YELLOW CLEAR CHIP SMD1 | $0.41 | 1 | $0.41 https://www.digikey.com/en/products/detail/kingbright/APHHS1005SYCK/1747503 https://app.ultralibrarian.com/details/f21eebf1-5907-11ee-9288-0ae0a3b49db5/Kingbright/APHHS1005CGCK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 - yellow SMD LED 0402 package for debug | NEW
Digikey | 754-2123-1-ND LED RED CLEAR 2SMD | 1 | $0.52 | 1 | $0.52 https://www.digikey.com/en/products/detail/kingbright/APHHS1005LSECK-J3-PF/7318976 https://app.ultralibrarian.com/details/f21eebf1-5907-11ee-9288-0ae0a3b49db5/Kingbright/APHHS1005CGCK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 - red SMD LED 0402 package for error indication | NEW
Digikey | 754-1503-1-ND LED GREEN CLEAR CHIP SMD1 | $0.70 | 1 | $0.70 https://www.digikey.com/en/products/detail/kingbright/APHHS1005ZGC/2263569 https://app.ultralibrarian.com/details/f21eebf1-5907-11ee-9288-0ae0a3b49db5/Kingbright/APHHS1005CGCK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 - green SMD LED 0402 package for debug | NEW
Digikey | 754-1504-1-ND LED BLUE CLEAR CHIP SMD 1 | $0.51 | 1 | $0.51 https://www.digikey.com/en/products/detail/kingbright/APHHS1005QBC-D/2263568 https://app.ultralibrarian.com/details/f21eebf1-5907-11ee-9288-0ae0a3b49db5/Kingbright/APHHS1005CGCK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 - blue SMD LED 0402 package for debug | NEW
Digikey | CAY16-1001F4LFCT-ND RES ARRAY 4 RES 1K OHM 12061 | $0.10 | 1 | $0.10 https://www.digikey.com/en/products/detail/bourns-inc/CAY16-1001F4LF/2566504 https://app.ultralibrarian.com/details/ccdadb33-1071-11e9-ab3a-0a3560a4cccc/Bourns-Electronics/CAY16-1001F4LF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 - 1k Ohm resistor array, 4 resistors
Digikey | 952-2664-1-ND PC TEST POINT NATURAL | 1 | $0.31 | | $0.00 https://www.digikey.com/en/products/detail/harwin-inc/S2751-46R/5250499 https://www.mouser.com/ProductDetail/Harwin/S2751-46R?qs=DaxoyN%2FvrebM3VuuS3MPNA%3D%3D - TH testpoint to probe mouse

Category | Vendor | Item Number
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

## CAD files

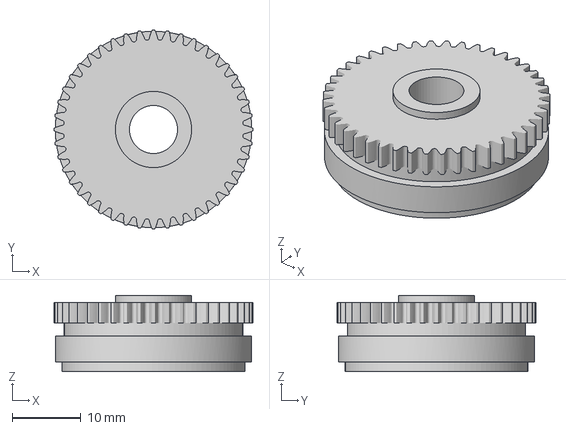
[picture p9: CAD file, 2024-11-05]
hardware/3d_print_mounts/wheel mount gears- large gear v1.3mf
29.0 x 29.0 x 11.1 mm

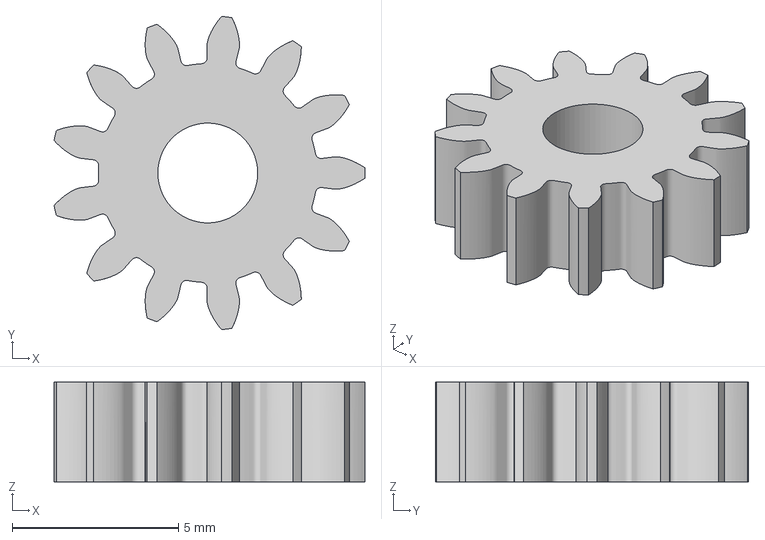
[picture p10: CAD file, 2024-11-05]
hardware/3d_print_mounts/wheel mount gears- small gear v2 v1.3mf
9.35 x 9.41 x 3.00 mm

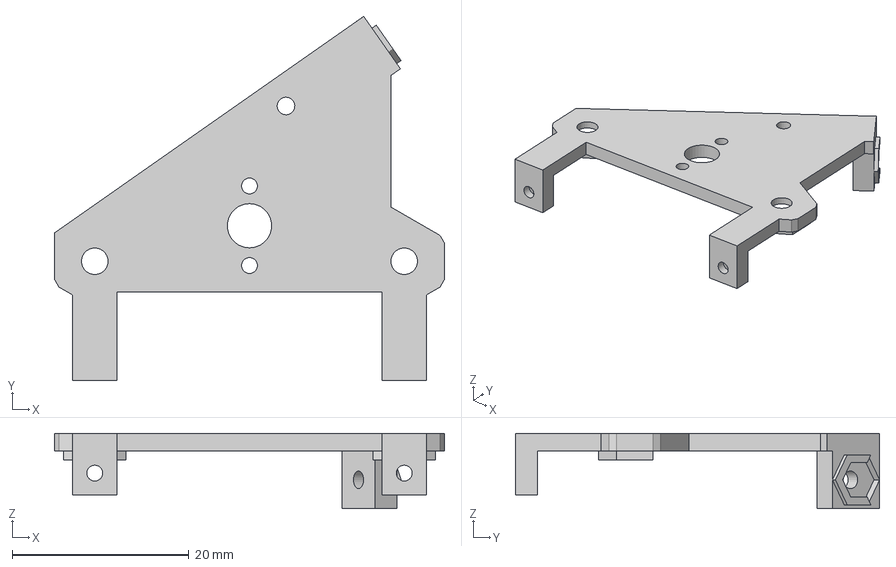
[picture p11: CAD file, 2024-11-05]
hardware/3d_print_mounts/wheel mount- right v2 v7.3mf
44.1 x 41.2 x 8.52 mm

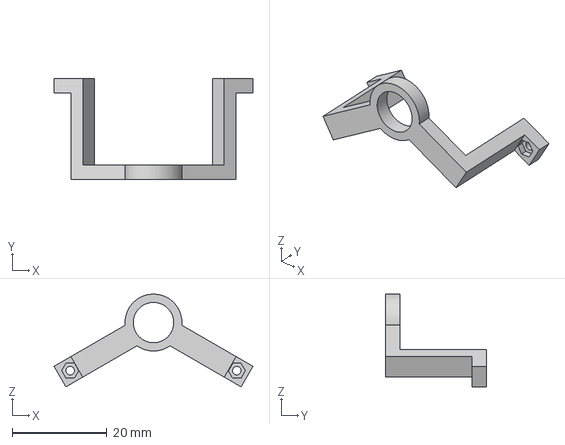
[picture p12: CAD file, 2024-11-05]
hardware/3d_print_mounts/vacuum motor mount 2 v5.3mf
41.9 x 21.2 x 19.5 mm

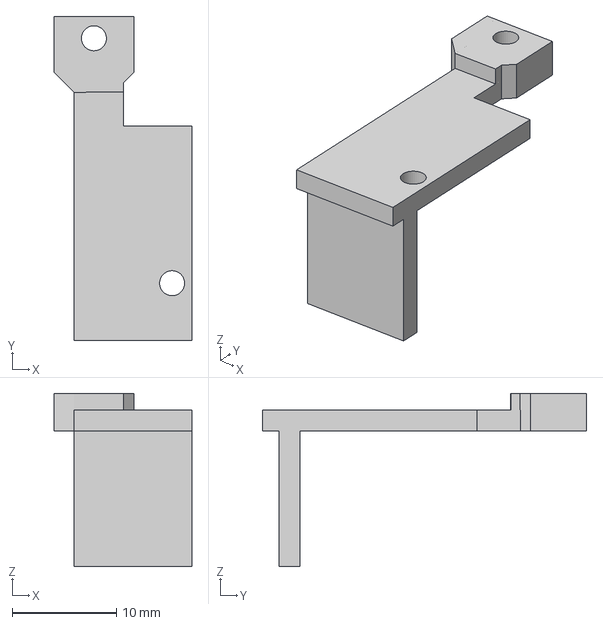
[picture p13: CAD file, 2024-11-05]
hardware/3d_print_mounts/sharp sensor mount 2.0 v7.3mf
13.2 x 31.1 x 16.6 mm

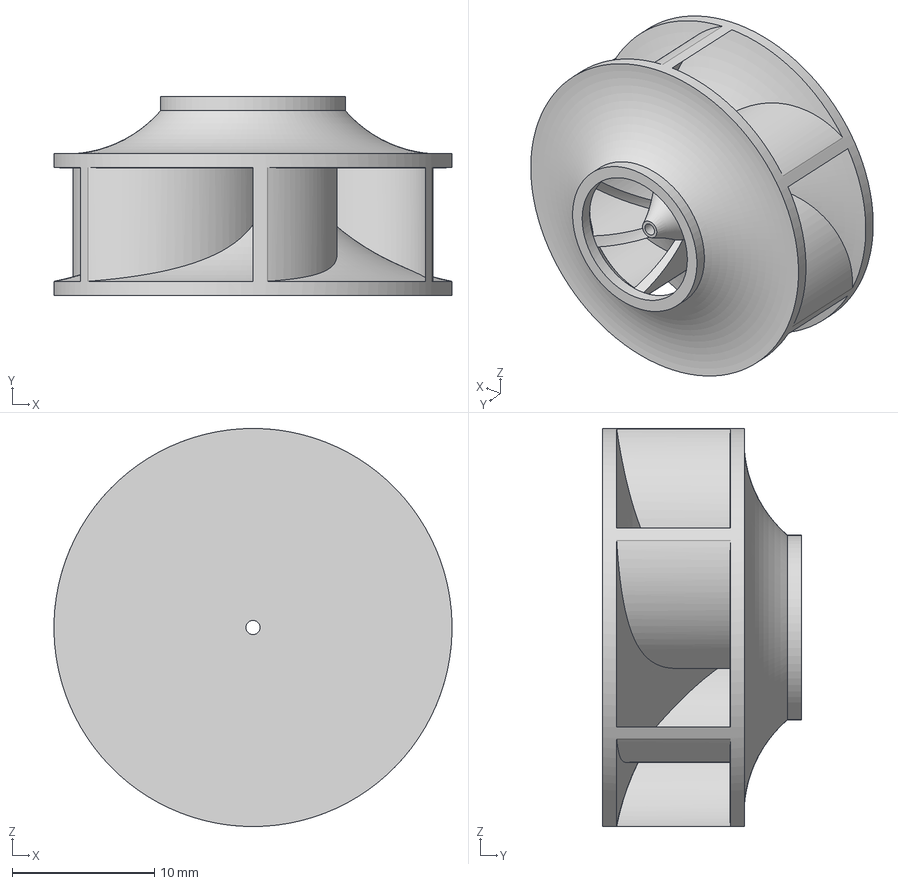
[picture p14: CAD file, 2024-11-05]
hardware/3d_print_mounts/vacuum fan 7 v2.3mf
28.0 x 14.0 x 28.0 mm

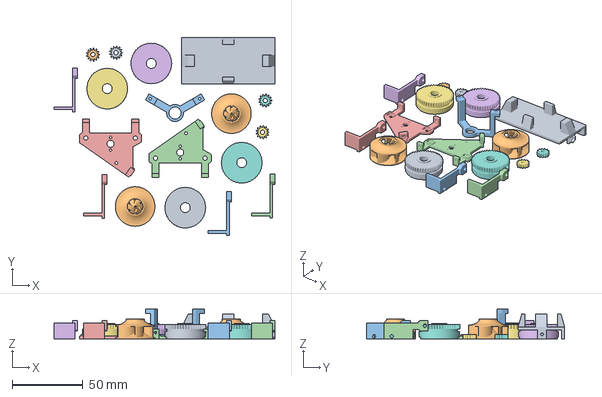
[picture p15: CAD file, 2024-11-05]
hardware/3d_print_mounts/Battery Mount- 450mAh LiPo v5.3mf
156.3 x 140.3 x 21.2 mm

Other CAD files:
hardware/3d_print_mounts/wheel mount- left v3.3mf

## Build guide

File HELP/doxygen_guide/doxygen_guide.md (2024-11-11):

# Doxygen Guide
Doxygen is a tool to automate documentation for software, including firmware written in C.

This guide will use Doxywizard and Graphviz to automate diagram generation.

## Let's Use Doxygen
Refer to Doxygen documentation to configure doxyfiles in detail... Otherwise, the steps include:

- Install Doxywizard and Graphviz
- Open Doxywizard and enter project directory path in the "specify the working directory" and "source code directory" boxes
- Create a new directory for Doxygen output documentation files and enter the path in the "destination directory" box
- Point to Graphviz binary Doxywizard's "Expert" tab -> "Dot" page
    - Required in the "DOT_PATH" and "DIA_PATH" boxes
- Configure Doxygen output as needed w/ everything else on Doxywizard- refer to example Doxyfile and Doxygen documentation
- Example doxyfile:
```
# Doxyfile 1.9.7

# This file describes the settings to be used by the documentation system
# doxygen (www.doxygen.org) for a project.
#
# All text after a double hash (##) is considered a comment and is placed in
# front of the TAG it is preceding.
#
# All text after a single hash (#) is considered a comment and will be ignored.
# The format is:
# TAG = value [value, ...]
# For lists, items can also be appended using:
# TAG += value [value, ...]
# Values that contain spaces should be placed between quotes (\" \").
#
# Note:
#
# Use doxygen to compare the used configuration file with the template
# configuration file:
# doxygen -x [configFile]
# Use doxygen to compare the used configuration file with the template
# configuration file without replacing the environment variables or CMake type
# replacement variables:
# doxygen -x_noenv [configFile]

#---------------------------------------------------------------------------
# Project related configuration options
#---------------------------------------------------------------------------

# This tag specifies the encoding used for all characters in the configuration
# file that follow. The default is UTF-8 which is also the encoding used for all
# text before the first occurrence of this tag. Doxygen uses libiconv (or the
# iconv built into libc) for the transcoding. See
# https://www.gnu.org/software/libiconv/ for the list of possible encodings.
# The default value is: UTF-8.

DOXYFILE_ENCODING      = UTF-8

# The PROJECT_NAME tag is a single word (or a sequence of words surrounded by
# double-quotes, unless you are using Doxywizard) that should identify the
# project for which the documentation is generated. This name is used in the
# title of most generated pages and in a few other places.
# The default value is: My Project.

PROJECT_NAME           = "project_name_here"

# The PROJECT_NUMBER tag can be used to enter a project or revision number. This
# could be handy for archiving the generated documentation or if some version
# control system is used.

PROJECT_NUMBER         =

# Using the PROJECT_BRIEF tag one can provide an optional one line description
# for a project that appears at the top of each page and should give viewer a
# quick idea about the purpose of the project. Keep the description short.

PROJECT_BRIEF          =

# With the PROJECT_LOGO tag one can specify a logo or an icon that is included
# in the documentation. The maximum height of the logo should not exceed 55
# pixels and the maximum width should not exceed 200 pixels. Doxygen will copy
# the logo to the output directory.

PROJECT_LOGO           =

# The OUTPUT_DIRECTORY tag is used to specify the (relative or absolute) path
# into which the generated documentation will be written. If a relative path is
# entered, it will be relative to the location where doxygen was started. If
# left blank the current directory will be used.

OUTPUT_DIRECTORY       = C:\output\directory\here

# If the CREATE_SUBDIRS tag is set to YES then doxygen will create up to 4096
# sub-directories (in 2 levels) under the output directory of each output format
# and will distribute the generated files over these directories. Enabling this
# option can be useful when feeding doxygen a huge amount of source files, where
# putting all generated files in the same directory would otherwise causes
# performance problems for the file system. Adapt CREATE_SUBDIRS_LEVEL to
# control the number of sub-directories.
# The default value is: NO.

CREATE_SUBDIRS         = NO

# Controls the number of sub-directories that will be created when
# CREATE_SUBDIRS tag is set to YES. Level 0 represents 16 directories, and every
# level increment doubles the number of directories, resulting in 4096
# directories at level 8 which is the default and also the maximum value. The
# sub-directories are organized in 2 levels, the first level always has a fixed
# number of 16 directories.
# Minimum value: 0, maximum value: 8, default value: 8.
# This tag requires that the tag CREATE_SUBDIRS is set to YES.

CREATE_SUBDIRS_LEVEL   = 8

# If the ALLOW_UNICODE_NAMES tag is set to YES, doxygen will allow non-ASCII
# characters to appear in the names of generated files. If set to NO, non-ASCII
# characters will be escaped, for example _xE3_x81_x84 will be used for Unicode
# U+3044.
# The default value is: NO.

ALLOW_UNICODE_NAMES    = NO

# The OUTPUT_LANGUAGE tag is used to specify the language in which all
# documentation generated by doxygen is written. Doxygen will use this
# information to generate all constant output in the proper language.
# Possible values are: Afrikaans, Arabic, Armenian, Brazilian, Bulgarian,
# Catalan, Chinese, Chinese-Traditional, Croatian, Czech, Danish, Dutch, English
# (United States), Esperanto, Farsi (Persian), Finnish, French, German, Greek,
# Hindi, Hungarian, Indonesian, Italian, Japanese, Japanese-en (Japanese with
# English messages), Korean, Korean-en (Korean with English messages), Latvian,
# Lithuanian, Macedonian, Norwegian, Persian (Farsi), Polish, Portuguese,
# Romanian, Russian, Serbian, Serbian-Cyrillic, Slovak, Slovene, Spanish,
# Swedish, Turkish, Ukrainian and Vietnamese.
# The default value is: English.

OUTPUT_LANGUAGE        = English

# If the BRIEF_MEMBER_DESC tag is set to YES, doxygen will include brief member
# descriptions after the members that are listed in the file and class
# documentation (similar to Javadoc). Set to NO to disable this.
# The default value is: YES.

BRIEF_MEMBER_DESC      = YES

# If the REPEAT_BRIEF tag is set to YES, doxygen will prepend the brief
# description of a member or function before the detailed description
#
# Note: If both HIDE_UNDOC_MEMBERS and BRIEF_MEMBER_DESC are set to NO, the
# brief descriptions will be completely suppressed.
# The default value is: YES.

REPEAT_BRIEF           = YES

# This tag implements a quasi-intelligent brief description abbreviator that is
# used to form the text in various listings. Each string in this list, if found
# as the leading text of the brief description, will be stripped from the text
# and the result, after processing the whole list, is used as the annotated
# text. Otherwise, the brief description is used as-is. If left blank, the
# following values are used ($name is automatically replaced with the name of
# the entity):The $name class, The $name widget, The $name file, is, provides,
# specifies, contains, represents, a, an and the.

ABBREVIATE_BRIEF       = "The $name class" \
                         "The $name widget" \
                         "The $name file" \
                         is \
                         provides \
                         specifies \
                         contains \
                         represents \
                         a \
                         an \
                         the

# If the ALWAYS_DETAILED_SEC and REPEAT_BRIEF tags are both set to YES then
# doxygen will generate a detailed section even if there is only a brief
# description.
# The default value is: NO.

ALWAYS_DETAILED_SEC    = NO

# If the INLINE_INHERITED_MEMB tag is set to YES, doxygen will show all
# inherited members of a class in the documentation of that class as if those
# members were ordinary class members. Constructors, destructors and assignment
# operators of the base classes will not be shown.
# The default value is: NO.

INLINE_INHERITED_MEMB  = NO

# If the FULL_PATH_NAMES tag is set to YES, doxygen will prepend the full path
# before files name in the file list and in the header files. If set to NO the
# shortest path that makes the file name unique will be used
# The default value is: YES.

FULL_PATH_NAMES        = YES

# The STRIP_FROM_PATH tag can be used to strip a user-defined part of the path.
# Stripping is only done if one of the specified strings matches the left-hand
# part of the path. The tag can be used to show relative paths in the file list.
# If left blank the directory from which doxygen is run is used as the path to
# strip.
#
# Note that you can specify absolute paths here, but also relative paths, which
# will be relative from the directory where doxygen is started.
# This tag requires that the tag FULL_PATH_NAMES is set to YES.

STRIP_FROM_PATH        =

# The STRIP_FROM_INC_PATH tag can be used to strip a user-defined part of the
# path mentioned in the documentation of a class, which tells the reader which
# header file to include in order to use a class. If left blank only the name of
# the header file containing the class definition is used. Otherwise one should
# specify the list of include paths that are normally passed to the compiler
# using the -I flag.

STRIP_FROM_INC_PATH    =

# If the SHORT_NAMES tag is set to YES, doxygen will generate much shorter (but
# less readable) file names. This can be useful is your file systems doesn't
# support long names like on DOS, Mac, or CD-ROM.
# The default value is: NO.

SHORT_NAMES            = NO

# If the JAVADOC_AUTOBRIEF tag is set to YES then doxygen will interpret the
# first line (until the first dot) of a Javadoc-style comment as the brief
# description. If set to NO, the Javadoc-style will behave just like regular Qt-
# style comments (thus requiring an explicit @brief command for a brief
# description.)
# The default value is: NO.

JAVADOC_AUTOBRIEF      = YES

# If the JAVADOC_BANNER tag is set to YES then doxygen will interpret a line
# such as
# /***************
# as being the beginning of a Javadoc-style comment "banner". If set to NO, the
# Javadoc-style will behave just like regular comments and it will not be
# interpreted by doxygen.
# The default value is: NO.

JAVADOC_BANNER         = YES

# If the QT_AUTOBRIEF tag is set to YES then doxygen will interpret the first
# line (until the first dot) of a Qt-style comment as the brief description. If
# set to NO, the Qt-style will behave just like regular Qt-style comments (thus
# requiring an explicit \brief command for a brief description.)
# The default value is: NO.

QT_AUTOBRIEF           = NO

# The MULTILINE_CPP_IS_BRIEF tag can be set to YES to make doxygen treat a
# multi-line C++ special comment block (i.e. a block of //! or /// comments) as
# a brief description. This used to be the default behavior. The new default is
# to treat a multi-line C++ comment block as a detailed description. Set this
# tag to YES if you prefer the old behavior instead.
#
# Note that setting this tag to YES also means that rational rose comments are
# not recognized any more.
# The default value is: NO.

MULTILINE_CPP_IS_BRIEF = NO

# By default Python docstrings are displayed as preformatted text and doxygen's
# special commands cannot be used. By setting PYTHON_DOCSTRING to NO the
# doxygen's special commands can be used and the contents of the docstring
# documentation blocks is shown as doxygen documentation.
# The default value is: YES.

PYTHON_DOCSTRING       = YES

# If the INHERIT_DOCS tag is set to YES then an undocumented member inherits the
# documentation from any documented member that it re-implements.
# The default value is: YES.

INHERIT_DOCS           = YES

# If the SEPARATE_MEMBER_PAGES tag is set to YES then doxygen will produce a new
# page for each member. If set to NO, the documentation of a member will be part
# of the file/class/namespace that contains it.
# The default value is: NO.

SEPARATE_MEMBER_PAGES  = NO

# The TAB_SIZE tag can be used to set the number of spaces in a tab. Doxygen
# uses this value to replace tabs by spaces in code fragments.
# Minimum value: 1, maximum value: 16, default value: 4.

TAB_SIZE               = 4

# This tag can be used to specify a number of aliases that act as commands in
# the documentation. An alias has the form:
# name=value
# For example adding
# "sideeffect=@par Side Effects:^^"
# will allow you to put the command \sideeffect (or @sideeffect) in the
# documentation, which will result in a user-defined paragraph with heading
# "Side Effects:". Note that you cannot put \n's in the value part of an alias
# to insert newlines (in the resulting output). You can put ^^ in the value part
# of an alias to insert a newline as if a physical newline was in the original
# file. When you need a literal { or } or , in the value part of an alias you
# have to escape them by means of a backslash (\), this can lead to conflicts
# with the commands \{ and \} for these it is advised to use the version @{ and
# @} or use a double escape (\\{ and \\})

ALIASES                =

# Set the OPTIMIZE_OUTPUT_FOR_C tag to YES if your project consists of C sources
# only. Doxygen will then generate output that is more tailored for C. For
# instance, some of the names that are used will be different. The list of all
# members will be omitted, etc.
# The default value is: NO.

OPTIMIZE_OUTPUT_FOR_C  = YES

# Set the OPTIMIZE_OUTPUT_JAVA tag to YES if your project consists of Java or
# Python sources only. Doxygen will then generate output that is more tailored
# for that language. For instance, namespaces will be presented as packages,
# qualified scopes will look different, etc.
# The default value is: NO.

OPTIMIZE_OUTPUT_JAVA   = NO

# Set the OPTIMIZE_FOR_FORTRAN tag to YES if your project consists of Fortran
# sources. Doxygen will then generate output that is tailored for Fortran.
# The default value is: NO.

OPTIMIZE_FOR_FORTRAN   = NO

# Set the OPTIMIZE_OUTPUT_VHDL tag to YES if your project consists of VHDL
# sources. Doxygen will then generate output that is tailored for VHDL.
# The default value is: NO.

OPTIMIZE_OUTPUT_VHDL   = NO

# Set the OPTIMIZE_OUTPUT_SLICE tag to YES if your project consists of Slice
# sources only. Doxygen will then generate output that is more tailored for that
# language. For instance, namespaces will be presented as modules, types will be
# separated into more groups, etc.
# The default value is: NO.

OPTIMIZE_OUTPUT_SLICE  = NO

# Doxygen selects the parser to use depending on the extension of the files it
# parses. With this tag you can assign which parser to use for a given
# extension. Doxygen has a built-in mapping, but you can override or extend it
# using this tag. The format is ext=language, where ext is a file extension, and
# language is one of the parsers supported by doxygen: IDL, Java, JavaScript,
# Csharp (C#), C, C++, Lex, D, PHP, md (Markdown), Objective-C, Python, Slice,
# VHDL, Fortran (fixed format Fortran: FortranFixed, free formatted Fortran:
# FortranFree, unknown formatted Fortran: Fortran. In the later case the parser
# tries to guess whether the code is fixed or free formatted code, this is the
# default for Fortran type files). For instance to make doxygen treat .inc files
# as Fortran files (default is PHP), and .f files as C (default is Fortran),
# use: inc=Fortran f=C.
#
# Note: For files without extension you can use no_extension as a placeholder.
#
# Note that for custom extensions you also need to set FILE_PATTERNS otherwise
# the files are not read by doxygen. When specifying no_extension you should add
# * to the FILE_PATTERNS.
#
# Note see also the list of default file extension mappings.

EXTENSION_MAPPING      =

# If the MARKDOWN_SUPPORT tag is enabled then doxygen pre-processes all comments
# according to the Markdown format, which allows for more readable
# documentation. See https://daringfireball.net/projects/markdown/ for details.
# The output of markdown processing is further processed by doxygen, so you can
# mix doxygen, HTML, and XML commands with Markdown formatting. Disable only in
# case of backward compatibilities issues.
# The default value is: YES.

MARKDOWN_SUPPORT       = YES

# When the TOC_INCLUDE_HEADINGS tag is set to a non-zero value, all headings up
# to that level are automatically included in the table of contents, even if
# they do not have an id attribute.
# Note: This feature currently applies only to Markdown headings.
# Minimum value: 0, maximum value: 99, default value: 5.
# This tag requires that the tag MARKDOWN_SUPPORT is set to YES.

TOC_INCLUDE_HEADINGS   = 5

# The MARKDOWN_ID_STYLE tag can be used to specify the algorithm used to
# generate identifiers for the Markdown headings. Note: Every identifier is
# unique.
# Possible values are: DOXYGEN Use a fixed 'autotoc_md' string followed by a
# sequence number starting at 0. and GITHUB Use the lower case version of title
# with any whitespace replaced by '-' and punctations characters removed..
# The default value is: DOXYGEN.
# This tag requires that the tag MARKDOWN_SUPPORT is set to YES.

MARKDOWN_ID_STYLE      = DOXYGEN

# When enabled doxygen tries to link words that correspond to documented
# classes, or namespaces to their corresponding documentation. Such a link can
# be prevented in individual cases by putting a % sign in front of the word or
# globally by setting AUTOLINK_SUPPORT to NO.
# The default value is: YES.

AUTOLINK_SUPPORT       = YES

# If you use STL classes (i.e. std::string, std::vector, etc.) but do not want
# to include (a tag file for) the STL sources as input, then you should set this
# tag to YES in order to let doxygen match functions declarations and
# definitions whose arguments contain STL classes (e.g. func(std::string);
# versus func(std::string) {}). This also make the inheritance and collaboration
# diagrams that involve STL classes more complete and accurate.
# The default value is: NO.

BUILTIN_STL_SUPPORT    = NO

# If you use Microsoft's C++/CLI language, you should set this option to YES to
# enable parsing support.
# The default value is: NO.

CPP_CLI_SUPPORT        = NO

# Set the SIP_SUPPORT tag to YES if your project consists of sip (see:
# https://www.riverbankcomputing.com/software/sip/intro) sources only. Doxygen
# will parse them like normal C++ but will assume all classes use public instead
# of private inheritance when no explicit protection keyword is present.
# The default value is: NO.

SIP_SUPPORT            = NO

# For Microsoft's IDL there are propget and propput attributes to indicate
# getter and setter methods for a property. Setting this option to YES will make
# doxygen to replace the get and set methods by a property in the documentation.
# This will only work if the methods are indeed getting or setting a simple
# type. If this is not the case, or you want to show the methods anyway, you
# should set this option to NO.
# The default value is: YES.

IDL_PROPERTY_SUPPORT   = YES

# If member grouping is used in the documentation and the DISTRIBUTE_GROUP_DOC
# tag is set to YES then doxygen will reuse the documentation of the first
# member in the group (if any) for the other members of the group. By default
# all members of a group must be documented explicitly.
# The default value is: NO.

DISTRIBUTE_GROUP_DOC   = NO

# If one adds a struct or class to a group and this option is enabled, then also
# any nested class or struct is added to the same group. By default this option
# is disabled and one has to add nested compounds explicitly via \ingroup.
# The default value is: NO.

GROUP_NESTED_COMPOUNDS = NO

# Set the SUBGROUPING tag to YES to allow class member groups of the same type
# (for instance a group of public functions) to be put as a subgroup of that
# type (e.g. under the Public Functions section). Set it to NO to prevent
# subgrouping. Alternatively, this can be done per class using the
# \nosubgrouping command.
# The default value is: YES.

SUBGROUPING            = YES

# When the INLINE_GROUPED_CLASSES tag is set to YES, classes, structs and unions
# are shown inside the group in which they are included (e.g. using \ingroup)
# instead of on a separate page (for HTML and Man pages) or section (for LaTeX
# and RTF).
#
# Note that this feature does not work in combination with
# SEPARATE_MEMBER_PAGES.
# The default value is: NO.

INLINE_GROUPED_CLASSES = NO

# When the INLINE_SIMPLE_STRUCTS tag is set to YES, structs, classes, and unions
# with only public data fields or simple typedef fields will be shown inline in
# the documentation of the scope in which they are defined (i.e. file,
# namespace, or group documentation), provided this scope is documented. If set
# to NO, structs, classes, and unions are shown on a separate page (for HTML and
# Man pages) or section (for LaTeX and RTF).
# The default value is: NO.

INLINE_SIMPLE_STRUCTS  = NO

# When TYPEDEF_HIDES_STRUCT tag is enabled, a typedef of a struct, union, or
# enum is documented as struct, union, or enum with the name of the typedef. So
# typedef struct TypeS {} TypeT, will appear in the documentation as a struct
# with name TypeT. When disabled the typedef will appear as a member of a file,
# namespace, or class. And the struct will be named TypeS. This can typically be
# useful for C code in case the coding convention dictates that all compound
# types are typedef'ed and only the typedef is referenced, never the tag name.
# The default value is: NO.

TYPEDEF_HIDES_STRUCT   = NO

# The size of the symbol lookup cache can be set using LOOKUP_CACHE_SIZE. This
# cache is used to resolve symbols given their name and scope. Since this can be
# an expensive process and often the same symbol appears multiple times in the
# code, doxygen keeps a cache of pre-resolved symbols. If the cache is too small
# doxygen will become slower. If the cache is too large, memory is wasted. The
# cache size is given by this formula: 2^(16+LOOKUP_CACHE_SIZE). The valid range
# is 0..9, the default is 0, corresponding to a cache size of 2^16=65536
# symbols. At the end of a run doxygen will report the cache usage and suggest
# the optimal cache size from a speed point of view.
# Minimum value: 0, maximum value: 9, default value: 0.

LOOKUP_CACHE_SIZE      = 0

# The NUM_PROC_THREADS specifies the number of threads doxygen is allowed to use
# during processing. When set to 0 doxygen will based this on the number of
# cores available in the system. You can set it explicitly to a value larger
# than 0 to get more control over the balance between CPU load and processing
# speed. At this moment only the input processing can be done using multiple
# threads. Since this is still an experimental feature the default is set to 1,
# which effectively disables parallel processing. Please report any issues you
# encounter. Generating dot graphs in parallel is controlled by the
# DOT_NUM_THREADS setting.
# Minimum value: 0, maximum value: 32, default value: 1.

NUM_PROC_THREADS       = 1

# If the TIMESTAMP tag is set different from NO then each generated page will
# contain the date or date and time when the page was generated. Setting this to
# NO can help when comparing the output of multiple runs.
# Possible values are: YES, NO, DATETIME and DATE.
# The default value is: NO.

TIMESTAMP              = NO

#---------------------------------------------------------------------------
# Build related configuration options
#---------------------------------------------------------------------------

# If the EXTRACT_ALL tag is set to YES, doxygen will assume all entities in
# documentation are documented, even if no documentation was available. Private
# class members and static file members will be hidden unless the
# EXTRACT_PRIVATE respectively EXTRACT_STATIC tags are set to YES.
# Note: This will also disable the warnings about undocumented members that are
# normally produced when WARNINGS is set to YES.
# The default value is: NO.

EXTRACT_ALL            = YES

# If the EXTRACT_PRIVATE tag is set to YES, all private members of a class will
# be included in the documentation.
# The default value is: NO.

EXTRACT_PRIVATE        = YES

# If the EXTRACT_PRIV_VIRTUAL tag is set to YES, documented private virtual
# methods of a class will be included in the documentation.
# The default value is: NO.

EXTRACT_PRIV_VIRTUAL   = YES

# If the EXTRACT_PACKAGE tag is set to YES, all members with package or internal
# scope will be included in the documentation.
# The default value is: NO.

EXTRACT_PACKAGE        = YES

# If the EXTRACT_STATIC tag is set to YES, all static members of a file will be
# included in the documentation.
# The default value is: NO.

EXTRACT_STATIC         = YES

# If the EXTRACT_LOCAL_CLASSES tag is set to YES, classes (and structs) defined
# locally in source files will be included in the documentation. If set to NO,
# only classes defined in header files are included. Does not have any effect
# for Java sources.
# The default value is: YES.

EXTRACT_LOCAL_CLASSES  = YES

# This flag is only useful for Objective-C code. If set to YES, local methods,
# which are defined in the implementation section but not in the interface are
# included in the documentation. If set to NO, only methods in the interface are
# included.
# The default value is: NO.

EXTRACT_LOCAL_METHODS  = YES

# If this flag is set to YES, the members of anonymous namespaces will be
# extracted and appear in the documentation as a namespace called
# 'anonymous_namespace{file}', where file will be replaced with the base name of
# the file that contains the anonymous namespace. By default anonymous namespace
# are hidden.
# The default value is: NO.

EXTRACT_ANON_NSPACES   = NO

# If this flag is set to YES, the name of an unnamed parameter in a declaration
# will be determined by the corresponding definition. By default unnamed
# parameters remain unnamed in the output.
# The default value is: YES.

RESOLVE_UNNAMED_PARAMS = YES

# If the HIDE_UNDOC_MEMBERS tag is set to YES, doxygen will hide all
# undocumented members inside documented classes or files. If set to NO these
# members will be included in the various overviews, but no documentation
# section is generated. This option has no effect if EXTRACT_ALL is enabled.
# The default value is: NO.

HIDE_UNDOC_MEMBERS     = NO

# If the HIDE_UNDOC_CLASSES tag is set to YES, doxygen will hide all
# undocumented classes that are normally visible in the class hierarchy. If set
# to NO, these classes will be included in the various overviews. This option
# will also hide undocumented C++ concepts if enabled. This option has no effect
# if EXTRACT_ALL is enabled.
# The default value is: NO.

HIDE_UNDOC_CLASSES     = NO

# If the HIDE_FRIEND_COMPOUNDS tag is set to YES, doxygen will hide all friend
# declarations. If set to NO, these declarations will be included in the
# documentation.
# The default value is: NO.

HIDE_FRIEND_COMPOUNDS  = NO

# If the HIDE_IN_BODY_DOCS tag is set to YES, doxygen will hide any
# documentation blocks found inside the body of a function. If set to NO, these
# blocks will be appended to the function's detailed documentation block.
# The default value is: NO.

HIDE_IN_BODY_DOCS      = NO

# The INTERNAL_DOCS tag determines if documentation that is typed after a
# \internal command is included. If the tag is set to NO then the documentation
# will be excluded. Set it to YES to include the internal documentation.
# The default value is: NO.

INTERNAL_DOCS          = NO

# With the correct setting of option CASE_SENSE_NAMES doxygen will better be
# able to match the capabilities of the underlying filesystem. In case the
# filesystem is case sensitive (i.e. it supports files in the same directory
# whose names only differ in casing), the option must be set to YES to properly
# deal with such files in case they appear in the input. For filesystems that
# are not case sensitive the option should be set to NO to properly deal with
# output files written for symbols that only differ in casing, such as for two
# classes, one named CLASS and the other named Class, and to also support
# references to files without having to specify the exact matching casing. On
# Windows (including Cygwin) and MacOS, users should typically set this option
# to NO, whereas on Linux or other Unix flavors it should typically be set to
# YES.
# Possible values are: SYSTEM, NO and YES.
# The default value is: SYSTEM.

CASE_SENSE_NAMES       = SYSTEM

# If the HIDE_SCOPE_NAMES tag is set to NO then doxygen will show members with
# their full class and namespace scopes in the documentation. If set to YES, the
# scope will be hidden.
# The default value is: NO.

HIDE_SCOPE_NAMES       = YES

# If the HIDE_COMPOUND_REFERENCE tag is set to NO (default) then doxygen will
# append additional text to a page's title, such as Class Reference. If set to
# YES the compound reference will be hidden.
# The default value is: NO.

HIDE_COMPOUND_REFERENCE= NO

# If the SHOW_HEADERFILE tag is set to YES then the documentation for a class
# will show which file needs to be included to use the class.
# The default value is: YES.

SHOW_HEADERFILE        = YES

# If the SHOW_INCLUDE_FILES tag is set to YES then doxygen will put a list of
# the files that are included by a file in the documentation of that file.
# The default value is: YES.

SHOW_INCLUDE_FILES     = YES

# If the SHOW_GROUPED_MEMB_INC tag is set to YES then Doxygen will add for each
# grouped member an include statement to the documentation, telling the reader
# which file to include in order to use the member.
# The default value is: NO.

SHOW_GROUPED_MEMB_INC  = NO

# If the FORCE_LOCAL_INCLUDES tag is set to YES then doxygen will list include
# files with double quotes in the documentation rather than with sharp brackets.
# The default value is: NO.

FORCE_LOCAL_INCLUDES   = NO

# If the INLINE_INFO tag is set to YES then a tag [inline] is inserted in the
# documentation for inline members.
# The default value is: YES.

INLINE_INFO            = YES

# If the SORT_MEMBER_DOCS tag is set to YES then doxygen will sort the
# (detailed) documentation of file and class members alphabetically by member
# name. If set to NO, the members will appear in declaration order.
# The default value is: YES.

SORT_MEMBER_DOCS       = YES

# If the SORT_BRIEF_DOCS tag is set to YES then doxygen will sort the brief
# descriptions of file, namespace and class members alphabetically by member
# name. If set to NO, the members will appear in declaration order. Note that
# this will also influence the order of the classes in the class list.
# The default value is: NO.

SORT_BRIEF_DOCS        = NO

# If the SORT_MEMBERS_CTORS_1ST tag is set to YES then doxygen will sort the
# (brief and detailed) documentation of class members so that constructors and
# destructors are listed first. If set to NO the constructors will appear in the
# respective orders defined by SORT_BRIEF_DOCS and SORT_MEMBER_DOCS.
# Note: If SORT_BRIEF_DOCS is set to NO this option is ignored for sorting brief
# member documentation.
# Note: If SORT_MEMBER_DOCS is set to NO this option is ignored for sorting
# detailed member documentation.
# The default value is: NO.

SORT_MEMBERS_CTORS_1ST = NO

# If the SORT_GROUP_NAMES tag is set to YES then doxygen will sort the hierarchy
# of group names into alphabetical order. If set to NO the group names will
# appear in their defined order.
# The default value is: NO.

SORT_GROUP_NAMES       = NO

# If the SORT_BY_SCOPE_NAME tag is set to YES, the class list will be sorted by
# fully-qualified names, including namespaces. If set to NO, the class list will
# be sorted only by class name, not including the namespace part.
# Note: This option is not very useful if HIDE_SCOPE_NAMES is set to YES.
# Note: This option applies only to the class list, not to the alphabetical
# list.
# The default value is: NO.

SORT_BY_SCOPE_NAME     = NO

# If the STRICT_PROTO_MATCHING option is enabled and doxygen fails to do proper
# type resolution of all parameters of a function it will reject a match between
# the prototype and the implementation of a member function even if there is
# only one candidate or it is obvious which candidate to choose by doing a
# simple string match. By disabling STRICT_PROTO_MATCHING doxygen will still
# accept a match between prototype and implementation in such cases.
# The default value is: NO.

STRICT_PROTO_MATCHING  = NO

# The GENERATE_TODOLIST tag can be used to enable (YES) or disable (NO) the todo
# list. This list is created by putting \todo commands in the documentation.
# The default value is: YES.

GENERATE_TODOLIST      = YES

# The GENERATE_TESTLIST tag can be used to enable (YES) or disable (NO) the test
# list. This list is created by putting \test commands in the documentation.
# The default value is: YES.

GENERATE_TESTLIST      = YES

# The GENERATE_BUGLIST tag can be used to enable (YES) or disable (NO) the bug
# list. This list is created by putting \bug commands in the documentation.
# The default value is: YES.

GENERATE_BUGLIST       = YES

# The GENERATE_DEPRECATEDLIST tag can be used to enable (YES) or disable (NO)
# the deprecated list. This list is created by putting \deprecated commands in
# the documentation.
# The default value is: YES.

GENERATE_DEPRECATEDLIST= YES

# The ENABLED_SECTIONS tag can be used to enable conditional documentation
# sections, marked by \if <section_label> ... \endif and \cond <section_label>
# ... \endcond blocks.

ENABLED_SECTIONS       =

# The MAX_INITIALIZER_LINES tag determines the maximum number of lines that the
# initial value of a variable or macro / define can have for it to appear in the
# documentation. If the initializer consists of more lines than specified here
# it will be hidden. Use a value of 0 to hide initializers completely. The
# appearance of the value of individual variables and macros / defines can be
# controlled using \showinitializer or \hideinitializer command in the
# documentation regardless of this setting.
# Minimum value: 0, maximum value: 10000, default value: 30.

MAX_INITIALIZER_LINES  = 30

# Set the SHOW_USED_FILES tag to NO to disable the list of files generated at
# the bottom of the documentation of classes and structs. If set to YES, the
# list will mention the files that were used to generate the documentation.
# The default value is: YES.

SHOW_USED_FILES        = YES

# Set the SHOW_FILES tag to NO to disable the generation of the Files page. This
# will remove the Files entry from the Quick Index and from the Folder Tree View
# (if specified).
# The default value is: YES.

SHOW_FILES             = YES

# Set the SHOW_NAMESPACES tag to NO to disable the generation of the Namespaces
# page. This will remove the Namespaces entry from the Quick Index and from the
# Folder Tree View (if specified).
# The default value is: YES.

SHOW_NAMESPACES        = YES

# The FILE_VERSION_FILTER tag can be used to specify a program or script that
# doxygen should invoke to get the current version for each file (typically from
# the version control system). Doxygen will invoke the program by executing (via
# popen()) the command command input-file, where command is the value of the
# FILE_VERSION_FILTER tag, and input-file is the name of an input file provided
# by doxygen. Whatever the program writes to standard output is used as the file
# version. For an example see the documentation.

FILE_VERSION_FILTER    =

# The LAYOUT_FILE tag can be used to specify a layout file which will be parsed
# by doxygen. The layout file controls the global structure of the generated
# output files in an output format independent way. To create the layout file
# that represents doxygen's defaults, run doxygen with the -l option. You can
# optionally specify a file name after the option, if omitted DoxygenLayout.xml
# will be used as the name of the layout file. See also section "Changing the
# layout of pages" for information.
#
# Note that if you run doxygen from a directory containing a file called
# DoxygenLayout.xml, doxygen will parse it automatically even if the LAYOUT_FILE
# tag is left empty.

LAYOUT_FILE            =

# The CITE_BIB_FILES tag can be used to specify one or more bib files containing
# the reference definitions. This must be a list of .bib files. The .bib
# extension is automatically appended if omitted. This requires the bibtex tool
# to be installed. See also https://en.wikipedia.org/wiki/BibTeX for more info.
# For LaTeX the style of the bibliography can be controlled using
# LATEX_BIB_STYLE. To use this feature you need bibtex and perl available in the
# search path. See also \cite for info how to create references.

CITE_BIB_FILES         =

#---------------------------------------------------------------------------
# Configuration options related to warning and progress messages
#---------------------------------------------------------------------------

# The QUIET tag can be used to turn on/off the messages that are generated to
# standard output by doxygen. If QUIET is set to YES this implies that the
# messages are off.
# The default value is: NO.

QUIET                  = NO

# The WARNINGS tag can be used to turn on/off the warning messages that are
# generated to standard error (stderr) by doxygen. If WARNINGS is set to YES
# this implies that the warnings are on.
#
# Tip: Turn warnings on while writing the documentation.
# The default value is: YES.

WARNINGS               = YES

# If the WARN_IF_UNDOCUMENTED tag is set to YES then doxygen will generate
# warnings for undocumented members. If EXTRACT_ALL is set to YES then this flag
# will automatically be disabled.
# The default value is: YES.

WARN_IF_UNDOCUMENTED   = YES

# If the WARN_IF_DOC_ERROR tag is set to YES, doxygen will generate warnings for
# potential errors in the documentation, such as documenting some parameters in
# a documented function twice, or documenting parameters that don't exist or
# using markup commands wrongly.
# The default value is: YES.

WARN_IF_DOC_ERROR      = YES

# If WARN_IF_INCOMPLETE_DOC is set to YES, doxygen will warn about incomplete
# function parameter documentation. If set to NO, doxygen will accept that some
# parameters have no documentation without warning.
# The default value is: YES.

WARN_IF_INCOMPLETE_DOC = YES

# This WARN_NO_PARAMDOC option can be enabled to get warnings for functions that
# are documented, but have no documentation for their parameters or return
# value. If set to NO, doxygen will only warn about wrong parameter
# documentation, but not about the absence of documentation. If EXTRACT_ALL is
# set to YES then this flag will automatically be disabled. See also
# WARN_IF_INCOMPLETE_DOC
# The default value is: NO.

WARN_NO_PARAMDOC       = NO

# If WARN_IF_UNDOC_ENUM_VAL option is set to YES, doxygen will warn about
# undocumented enumeration values. If set to NO, doxygen will accept
# undocumented enumeration values. If EXTRACT_ALL is set to YES then this flag
# will automatically be disabled.
# The default value is: NO.

WARN_IF_UNDOC_ENUM_VAL = NO

# If the WARN_AS_ERROR tag is set to YES then doxygen will immediately stop when
# a warning is encountered. If the WARN_AS_ERROR tag is set to FAIL_ON_WARNINGS
# then doxygen will continue running as if WARN_AS_ERROR tag is set to NO, but
# at the end of the doxygen process doxygen will return with a non-zero status.
# If the WARN_AS_ERROR tag is set to FAIL_ON_WARNINGS_PRINT then doxygen behaves
# like FAIL_ON_WARNINGS but in case no WARN_LOGFILE is defined doxygen will not
# write the warning messages in between other messages but write them at the end
# of a run, in case a WARN_LOGFILE is defined the warning messages will be
# besides being in the defined file also be shown at the end of a run, unless
# the WARN_LOGFILE is defined as - i.e. standard output (stdout) in that case
# the behavior will remain as with the setting FAIL_ON_WARNINGS.
# Possible values are: NO, YES, FAIL_ON_WARNINGS and FAIL_ON_WARNINGS_PRINT.
# The default value is: NO.

WARN_AS_ERROR          = NO

# The WARN_FORMAT tag determines the format of the warning messages that doxygen
# can produce. The string should contain the $file, $line, and $text tags, which
# will be replaced by the file and line number from which the warning originated
# and the warning text. Optionally the format may contain $version, which will
# be replaced by the version of the file (if it could be obtained via
# FILE_VERSION_FILTER)
# See also: WARN_LINE_FORMAT
# The default value is: $file:$line: $text.

WARN_FORMAT            = "$file:$line: $text"

# In the $text part of the WARN_FORMAT command it is possible that a reference
# to a more specific place is given. To make it easier to jump to this place
# (outside of doxygen) the user can define a custom "cut" / "paste" string.
# Example:
# WARN_LINE_FORMAT = "'vi $file +$line'"
# See also: WARN_FORMAT
# The default value is: at line $line of file $file.

WARN_LINE_FORMAT       = "at line $line of file $file"

# The WARN_LOGFILE tag can be used to specify a file to which warning and error
# messages should be written. If left blank the output is written to standard
# error (stderr). In case the file specified cannot be opened for writing the
# warning and error messages are written to standard error. When as file - is
# specified the warning and error messages are written to standard output
# (stdout).

WARN_LOGFILE           =

#---------------------------------------------------------------------------
# Configuration options related to the input files
#---------------------------------------------------------------------------

# The INPUT tag is used to specify the files and/or directories that contain
# documented source files. You may enter file names like myfile.cpp or
# directories like /usr/src/myproject. Separate the files or directories with
# spaces. See also FILE_PATTERNS and EXTENSION_MAPPING
# Note: If this tag is empty the current directory is searched.

INPUT                  = C:\input\diretory\here

# This tag can be used to specify the character encoding of the source files
# that doxygen parses. Internally doxygen uses the UTF-8 encoding. Doxygen uses
# libiconv (or the iconv built into libc) for the transcoding. See the libiconv
# documentation (see:
# https://www.gnu.org/software/libiconv/) for the list of possible encodings.
# See also: INPUT_FILE_ENCODING
# The default value is: UTF-8.

INPUT_ENCODING         = UTF-8

# This tag can be used to specify the character encoding of the source files
# that doxygen parses The INPUT_FILE_ENCODING tag can be used to specify
# character encoding on a per file pattern basis. Doxygen will compare the file
# name with each pattern and apply the encoding instead of the default
# INPUT_ENCODING) if there is a match. The character encodings are a list of the
# form: pattern=encoding (like *.php=ISO-8859-1). See cfg_input_encoding
# "INPUT_ENCODING" for further information on supported encodings.

INPUT_FILE_ENCODING    =

# If the value of the INPUT tag contains directories, you can use the
# FILE_PATTERNS tag to specify one or more wildcard patterns (like *.cpp and
# *.h) to filter out the source-files in the directories.
#
# Note that for custom extensions or not directly supported extensions you also
# need to set EXTENSION_MAPPING for the extension otherwise the files are not
# read by doxygen.
#
# Note the list of default checked file patterns might differ from the list of
# default file extension mappings.
#
# If left blank the following patterns are tested:*.c, *.cc, *.cxx, *.cpp,
# *.c++, *.java, *.ii, *.ixx, *.ipp, *.i++, *.inl, *.idl, *.ddl, *.odl, *.h,
# *.hh, *.hxx, *.hpp, *.h++, *.l, *.cs, *.d, *.php, *.php4, *.php5, *.phtml,
# *.inc, *.m, *.markdown, *.md, *.mm, *.dox (to be provided as doxygen C
# comment), *.py, *.pyw, *.f90, *.f95, *.f03, *.f08, *.f18, *.f, *.for, *.vhd,
# *.vhdl, *.ucf, *.qsf and *.ice.

FILE_PATTERNS          = *.c \
                         *.cc \
                         *.cxx \
                         *.cpp \
                         *.c++ \
                         *.java \
                         *.ii \
                         *.ixx \
                         *.ipp \
                         *.i++ \
                         *.inl \
                         *.idl \
                         *.ddl \
                         *.odl \
                         *.h \
                         *.hh \
                         *.hxx \
                         *.hpp \
                         *.h++ \
                         *.l \
                         *.cs \
                         *.d \
                         *.php \
                         *.php4 \
                         *.php5 \
                         *.phtml \
                         *.inc \
                         *.m \
                         *.markdown \
                         *.md \
                         *.mm \
                         *.dox \
                         *.py \
                         *.pyw \
                         *.f90 \
                         *.f95 \
                         *.f03 \
                         *.f08 \
                         *.f18 \
                         *.f \
                         *.for \
                         *.vhd \
                         *.vhdl \
                         *.ucf \
                         *.qsf \
                         *.ice

# The RECURSIVE tag can be used to specify whether or not subdirectories should
# be searched for input files as well.
# The default value is: NO.

RECURSIVE              = YES

# The EXCLUDE tag can be used to specify files and/or directories that should be
# excluded from the INPUT source files. This way you can easily exclude a
# subdirectory from a directory tree whose root is specified with the INPUT tag.
#
# Note that relative paths are relative to the directory from which doxygen is
# run.

EXCLUDE                =

# The EXCLUDE_SYMLINKS tag can be used to select whether or not files or
# directories that are symbolic links (a Unix file system feature) are excluded
# from the input.
# The default value is: NO.

EXCLUDE_SYMLINKS       = NO

# If the value of the INPUT tag contains directories, you can use the
# EXCLUDE_PATTERNS tag to specify one or more wildcard patterns to exclude
# certain files from those directories.
#
# Note that the wildcards are matched against the file with absolute path, so to
# exclude all test directories for example use the pattern */test/*

EXCLUDE_PATTERNS       =

# The EXCLUDE_SYMBOLS tag can be used to specify one or more symbol names
# (namespaces, classes, functions, etc.) that should be excluded from the
# output. The symbol name can be a fully qualified name, a word, or if the
# wildcard * is used, a substring. Examples: ANamespace, AClass,
# ANamespace::AClass, ANamespace::*Test

EXCLUDE_SYMBOLS        =

# The EXAMPLE_PATH tag can be used to specify one or more files or directories
# that contain example code fragments that are included (see the \include
# command).

EXAMPLE_PATH           =

# If the value of the EXAMPLE_PATH tag contains directories, you can use the
# EXAMPLE_PATTERNS tag to specify one or more wildcard pattern (like *.cpp and
# *.h) to filter out the source-files in the directories. If left blank all
# files are included.

EXAMPLE_PATTERNS       = *

# If the EXAMPLE_RECURSIVE tag is set to YES then subdirectories will be
# searched for input files to be used with the \include or \dontinclude commands
# irrespective of the value of the RECURSIVE tag.
# The default value is: NO.

EXAMPLE_RECURSIVE      = NO

# The IMAGE_PATH tag can be used to specify one or more files or directories
# that contain images that are to be included in the documentation (see the
# \image command).

IMAGE_PATH             =

# The INPUT_FILTER tag can be used to specify a program that doxygen should
# invoke to filter for each input file. Doxygen will invoke the filter program
# by executing (via popen()) the command:
#
# <filter> <input-file>
#
# where <filter> is the value of the INPUT_FILTER tag, and <input-file> is the
# name of an input file. Doxygen will then use the output that the filter
# program writes to standard output. If FILTER_PATTERNS is specified, this tag
# will be ignored.
#
# Note that the filter must not add or remove lines; it is applied before the
# code is scanned, but not when the output code is generated. If lines are added
# or removed, the anchors will not be placed correctly.
#
# Note that doxygen will use the data processed and written to standard output
# for further processing, therefore nothing else, like debug statements or used
# commands (so in case of a Windows batch file always use @echo OFF), should be
# written to standard output.
#
# Note that for custom extensions or not directly supported extensions you also
# need to set EXTENSION_MAPPING for the extension otherwise the files are not
# properly processed by doxygen.

INPUT_FILTER           =

# The FILTER_PATTERNS tag can be used to specify filters on a per file pattern
# basis. Doxygen will compare the file name with each pattern and apply the
# filter if there is a match. The filters are a list of the form: pattern=filter
# (like *.cpp=my_cpp_filter). See INPUT_FILTER for further information on how
# filters are used. If the FILTER_PATTERNS tag is empty or if none of the
# patterns match the file name, INPUT_FILTER is applied.
#
# Note that for custom extensions or not directly supported extensions you also
# need to set EXTENSION_MAPPING for the extension otherwise the files are not
# properly processed by doxygen.

FILTER_PATTERNS        =

# If the FILTER_SOURCE_FILES tag is set to YES, the input filter (if set using
# INPUT_FILTER) will also be used to filter the input files that are used for
# producing the source files to browse (i.e. when SOURCE_BROWSER is set to YES).
# The default value is: NO.

FILTER_SOURCE_FILES    = NO

# The FILTER_SOURCE_PATTERNS tag can be used to specify source filters per file
# pattern. A pattern will override the setting for FILTER_PATTERN (if any) and
# it is also possible to disable source filtering for a specific pattern using
# *.ext= (so without naming a filter).
# This tag requires that the tag FILTER_SOURCE_FILES is set to YES.

FILTER_SOURCE_PATTERNS =

# If the USE_MDFILE_AS_MAINPAGE tag refers to the name of a markdown file that
# is part of the input, its contents will be placed on the main page
# (index.html). This can be useful if you have a project on for instance GitHub
# and want to reuse the introduction page also for the doxygen output.

USE_MDFILE_AS_MAINPAGE =

# The Fortran standard specifies that for fixed formatted Fortran code all
# characters from position 72 are to be considered as comment. A common
# extension is to allow longer lines before the automatic comment starts. The
# setting FORTRAN_COMMENT_AFTER will also make it possible that longer lines can
# be processed before the automatic comment starts.
# Minimum value: 7, maximum value: 10000, default value: 72.

FORTRAN_COMMENT_AFTER  = 72

#---------------------------------------------------------------------------
# Configuration options related to source browsing
#---------------------------------------------------------------------------

# If the SOURCE_BROWSER tag is set to YES then a list of source files will be
# generated. Documented entities will be cross-referenced with these sources.
#
# Note: To get rid of all source code in the generated output, make sure that
# also VERBATIM_HEADERS is set to NO.
# The default value is: NO.

SOURCE_BROWSER         = NO

# Setting the INLINE_SOURCES tag to YES will include the body of functions,
# classes and enums directly into the documentation.
# The default value is: NO.

INLINE_SOURCES         = NO

# Setting the STRIP_CODE_COMMENTS tag to YES will instruct doxygen to hide any
# special comment blocks from generated source code fragments. Normal C, C++ and
# Fortran comments will always remain visible.
# The default value is: YES.

STRIP_CODE_COMMENTS    = YES

# If the REFERENCED_BY_RELATION tag is set to YES then for each documented
# entity all documented functions referencing it will be listed.
# The default value is: NO.

REFERENCED_BY_RELATION = NO

# If the REFERENCES_RELATION tag is set to YES then for each documented function
# all documented entities called/used by that function will be listed.
# The default value is: NO.

REFERENCES_RELATION    = NO

# If the REFERENCES_LINK_SOURCE tag is set to YES and SOURCE_BROWSER tag is set
# to YES then the hyperlinks from functions in REFERENCES_RELATION and
# REFERENCED_BY_RELATION lists will link to the source code. Otherwise they will
# link to the documentation.
# The default value is: YES.

REFERENCES_LINK_SOURCE = YES

# If SOURCE_TOOLTIPS is enabled (the default) then hovering a hyperlink in the
# source code will show a tooltip with additional information such as prototype,
# brief description and links to the definition and documentation. Since this
# will make the HTML file larger and loading of large files a bit slower, you
# can opt to disable this feature.
# The default value is: YES.
# This tag requires that the tag SOURCE_BROWSER is set to YES.

SOURCE_TOOLTIPS        = YES

# If the USE_HTAGS tag is set to YES then the references to source code will
# point to the HTML generated by the htags(1) tool instead of doxygen built-in
# source browser. The htags tool is part of GNU's global source tagging system
# (see https://www.gnu.org/software/global/global.html). You will need version
# 4.8.6 or higher.
#
# To use it do the following:
# - Install the latest version of global
# - Enable SOURCE_BROWSER and USE_HTAGS in the configuration file
# - Make sure the INPUT points to the root of the source tree
# - Run doxygen as normal
#
# Doxygen will invoke htags (and that will in turn invoke gtags), so these
# tools must be available from the command line (i.e. in the search path).
#
# The result: instead of the source browser generated by doxygen, the links to
# source code will now point to the output of htags.
# The default value is: NO.
# This tag requires that the tag SOURCE_BROWSER is set to YES.

USE_HTAGS              = NO

# If the VERBATIM_HEADERS tag is set the YES then doxygen will generate a
# verbatim copy of the header file for each class for which an include is
# specified. Set to NO to disable this.
# See also: Section \class.
# The default value is: YES.

VERBATIM_HEADERS       = YES

# If the CLANG_ASSISTED_PARSING tag is set to YES then doxygen will use the
# clang parser (see:
# http://clang.llvm.org/) for more accurate parsing at the cost of reduced
# performance. This can be particularly helpful with template rich C++ code for
# which doxygen's built-in parser lacks the necessary type information.
# Note: The availability of this option depends on whether or not doxygen was
# generated with the -Duse_libclang=ON option for CMake.
# The default value is: NO.

CLANG_ASSISTED_PARSING = NO

# If the CLANG_ASSISTED_PARSING tag is set to YES and the CLANG_ADD_INC_PATHS
# tag is set to YES then doxygen will add the directory of each input to the
# include path.
# The default value is: YES.
# This tag requires that the tag CLANG_ASSISTED_PARSING is set to YES.

CLANG_ADD_INC_PATHS    = YES

# If clang assisted parsing is enabled you can provide the compiler with command
# line options that you would normally use when invoking the compiler. Note that
# the include paths will already be set by doxygen for the files and directories
# specified with INPUT and INCLUDE_PATH.
# This tag requires that the tag CLANG_ASSISTED_PARSING is set to YES.

CLANG_OPTIONS          =

# If clang assisted parsing is enabled you can provide the clang parser with the
# path to the directory containing a file called compile_commands.json. This
# file is the compilation database (see:
# http://clang.llvm.org/docs/HowToSetupToolingForLLVM.html) containing the
# options used when the source files were built. This is equivalent to
# specifying the -p option to a clang tool, such as clang-check. These options
# will then be passed to the parser. Any options specified with CLANG_OPTIONS
# will be added as well.
# Note: The availability of this option depends on whether or not doxygen was
# generated with the -Duse_libclang=ON option for CMake.

CLANG_DATABASE_PATH    =

#---------------------------------------------------------------------------
# Configuration options related to the alphabetical class index
#---------------------------------------------------------------------------

# If the ALPHABETICAL_INDEX tag is set to YES, an alphabetical index of all
# compounds will be generated. Enable this if the project contains a lot of
# classes, structs, unions or interfaces.
# The default value is: YES.

ALPHABETICAL_INDEX     = YES

# The IGNORE_PREFIX tag can be used to specify a prefix (or a list of prefixes)
# that should be ignored while generating the index headers. The IGNORE_PREFIX
# tag works for classes, function and member names. The entity will be placed in
# the alphabetical list under the first letter of the entity name that remains
# after removing the prefix.
# This tag requires that the tag ALPHABETICAL_INDEX is set to YES.

IGNORE_PREFIX          =

#---------------------------------------------------------------------------
# Configuration options related to the HTML output
#---------------------------------------------------------------------------

# If the GENERATE_HTML tag is set to YES, doxygen will generate HTML output
# The default value is: YES.

GENERATE_HTML          = YES

# The HTML_OUTPUT tag is used to specify where the HTML docs will be put. If a
# relative path is entered the value of OUTPUT_DIRECTORY will be put in front of
# it.
# The default directory is: html.
# This tag requires that the tag GENERATE_HTML is set to YES.

HTML_OUTPUT            = html

# The HTML_FILE_EXTENSION tag can be used to specify the file extension for each
# generated HTML page (for example: .htm, .php, .asp).
# The default value is: .html.
# This tag requires that the tag GENERATE_HTML is set to YES.

HTML_FILE_EXTENSION    = .html

# The HTML_HEADER tag can be used to specify a user-defined HTML header file for
# each generated HTML page. If the tag is left blank doxygen will generate a
# standard header.
#
# To get valid HTML the header file that includes any scripts and style sheets
# that doxygen needs, which is dependent on the configuration options used (e.g.
# the setting GENERATE_TREEVIEW). It is highly recommended to start with a
# default header using
# doxygen -w html new_header.html new_footer.html new_stylesheet.css
# YourConfigFile
# and then modify the file new_header.html. See also section "Doxygen usage"
# for information on how to generate the default header that doxygen normally
# uses.
# Note: The header is subject to change so you typically have to regenerate the
# default header when upgrading to a newer version of doxygen. For a description
# of the possible markers and block names see the documentation.
# This tag requires that the tag GENERATE_HTML is set to YES.

HTML_HEADER            =

# The HTML_FOOTER tag can be used to specify a user-defined HTML footer for each
# generated HTML page. If the tag is left blank doxygen will generate a standard
# footer. See HTML_HEADER for more information on how to generate a default
# footer and what special commands can be used inside the footer. See also
# section "Doxygen usage" for information on how to generate the default footer
# that doxygen normally uses.
# This tag requires that the tag GENERATE_HTML is set to YES.

HTML_FOOTER            =

# The HTML_STYLESHEET tag can be used to specify a user-defined cascading style
# sheet that is used by each HTML page. It can be used to fine-tune the look of
# the HTML output. If left blank doxygen will generate a default style sheet.
# See also section "Doxygen usage" for information on how to generate the style
# sheet that doxygen normally uses.
# Note: It is recommended to use HTML_EXTRA_STYLESHEET instead of this tag, as
# it is more robust and this tag (HTML_STYLESHEET) will in the future become
# obsolete.
# This tag requires that the tag GENERATE_HTML is set to YES.

HTML_STYLESHEET        =

# The HTML_EXTRA_STYLESHEET tag can be used to specify additional user-defined
# cascading style sheets that are included after the standard style sheets
# created by doxygen. Using this option one can overrule certain style aspects.
# This is preferred over using HTML_STYLESHEET since it does not replace the
# standard style sheet and is therefore more robust against future updates.
# Doxygen will copy the style sheet files to the output directory.
# Note: The order of the extra style sheet files is of importance (e.g. the last
# style sheet in the list overrules the setting of the previous ones in the
# list).
# Note: Since the styling of scrollbars can currently not be overruled in
# Webkit/Chromium, the styling will be left out of the default doxygen.css if
# one or more extra stylesheets have been specified. So if scrollbar
# customization is desired it has to be added explicitly. For an example see the
# documentation.
# This tag requires that the tag GENERATE_HTML is set to YES.

HTML_EXTRA_STYLESHEET  =

# The HTML_EXTRA_FILES tag can be used to specify one or more extra images or
# other source files which should be copied to the HTML output directory. Note
# that these files will be copied to the base HTML output directory. Use the
# $relpath^ marker in the HTML_HEADER and/or HTML_FOOTER files to load these
# files. In the HTML_STYLESHEET file, use the file name only. Also note that the
# files will be copied as-is; there are no commands or markers available.
# This tag requires that the tag GENERATE_HTML is set to YES.

HTML_EXTRA_FILES       =

# The HTML_COLORSTYLE tag can be used to specify if the generated HTML output
# should be rendered with a dark or light theme.
# Possible values are: LIGHT always generate light mode output, DARK always
# generate dark mode output, AUTO_LIGHT automatically set the mode according to
# the user preference, use light mode if no preference is set (the default),
# AUTO_DARK automatically set the mode according to the user preference, use
# dark mode if no preference is set and TOGGLE allow to user to switch between
# light and dark mode via a button.
# The default value is: AUTO_LIGHT.
# This tag requires that the tag GENERATE_HTML is set to YES.

HTML_COLORSTYLE        = AUTO_LIGHT

# The HTML_COLORSTYLE_HUE tag controls the color of the HTML output. Doxygen
# will adjust the colors in the style sheet and background images according to
# this color. Hue is specified as an angle on a color-wheel, see
# https://en.wikipedia.org/wiki/Hue for more information. For instance the value
# 0 represents red, 60 is yellow, 120 is green, 180 is cyan, 240 is blue, 300
# purple, and 360 is red again.
# Minimum value: 0, maximum value: 359, default value: 220.
# This tag requires that the tag GENERATE_HTML is set to YES.

HTML_COLORSTYLE_HUE    = 220

# The HTML_COLORSTYLE_SAT tag controls the purity (or saturation) of the colors
# in the HTML output. For a value of 0 the output will use gray-scales only. A
# value of 255 will produce the most vivid colors.
# Minimum value: 0, maximum value: 255, default value: 100.
# This tag requires that the tag GENERATE_HTML is set to YES.

HTML_COLORSTYLE_SAT    = 100

# The HTML_COLORSTYLE_GAMMA tag controls the gamma correction applied to the
# luminance component of the colors in the HTML output. Values below 100
# gradually make the output lighter, whereas values above 100 make the output
# darker. The value divided by 100 is the actual gamma applied, so 80 represents
# a gamma of 0.8, The value 220 represents a gamma of 2.2, and 100 does not
# change the gamma.
# Minimum value: 40, maximum value: 240, default value: 80.
# This tag requires that the tag GENERATE_HTML is set to YES.

HTML_COLORSTYLE_GAMMA  = 80

# If the HTML_DYNAMIC_MENUS tag is set to YES then the generated HTML
# documentation will contain a main index with vertical navigation menus that
# are dynamically created via JavaScript. If disabled, the navigation index will
# consists of multiple levels of tabs that are statically embedded in every HTML
# page. Disable this option to support browsers that do not have JavaScript,
# like the Qt help browser.
# The default value is: YES.
# This tag requires that the tag GENERATE_HTML is set to YES.

HTML_DYNAMIC_MENUS     = YES

# If the HTML_DYNAMIC_SECTIONS tag is set to YES then the generated HTML
# documentation will contain sections that can be hidden and shown after the
# page has loaded.
# The default value is: NO.
# This tag requires that the tag GENERATE_HTML is set to YES.

HTML_DYNAMIC_SECTIONS  = NO

# With HTML_INDEX_NUM_ENTRIES one can control the preferred number of entries
# shown in the various tree structured indices initially; the user can expand
# and collapse entries dynamically later on. Doxygen will expand the tree to
# such a level that at most the specified number of entries are visible (unless
# a fully collapsed tree already exceeds this amount). So setting the number of
# entries 1 will produce a full collapsed tree by default. 0 is a special value
# representing an infinite number of entries and will result in a full expanded
# tree by default.
# Minimum value: 0, maximum value: 9999, default value: 100.
# This tag requires that the tag GENERATE_HTML is set to YES.

HTML_INDEX_NUM_ENTRIES = 9999

# If the GENERATE_DOCSET tag is set to YES, additional index files will be
# generated that can be used as input for Apple's Xcode 3 integrated development
# environment (see:
# https://developer.apple.com/xcode/), introduced with OSX 10.5 (Leopard). To
# create a documentation set, doxygen will generate a Makefile in the HTML
# output directory. Running make will produce the docset in that directory and
# running make install will install the docset in
# ~/Library/Developer/Shared/Documentation/DocSets so that Xcode will find it at
# startup. See https://developer.apple.com/library/archive/featuredarticles/Doxy
# genXcode/_index.html for more information.
# The default value is: NO.
# This tag requires that the tag GENERATE_HTML is set to YES.

GENERATE_DOCSET        = NO

# This tag determines the name of the docset feed. A documentation feed provides
# an umbrella under which multiple documentation sets from a single provider
# (such as a company or product suite) can be grouped.
# The default value is: Doxygen generated docs.
# This tag requires that the tag GENERATE_DOCSET is set to YES.

DOCSET_FEEDNAME        = "Doxygen generated docs"

# This tag determines the URL of the docset feed. A documentation feed provides
# an umbrella under which multiple documentation sets from a single provider
# (such as a company or product suite) can be grouped.
# This tag requires that the tag GENERATE_DOCSET is set to YES.

DOCSET_FEEDURL         =

# This tag specifies a string that should uniquely identify the documentation
# set bundle. This should be a reverse domain-name style string, e.g.
# com.mycompany.MyDocSet. Doxygen will append .docset to the name.
# The default value is: org.doxygen.Project.
# This tag requires that the tag GENERATE_DOCSET is set to YES.

DOCSET_BUNDLE_ID       = org.doxygen.Project

# The DOCSET_PUBLISHER_ID tag specifies a string that should uniquely identify
# the documentation publisher. This should be a reverse domain-name style
# string, e.g. com.mycompany.MyDocSet.documentation.
# The default value is: org.doxygen.Publisher.
# This tag requires that the tag GENERATE_DOCSET is set to YES.

DOCSET_PUBLISHER_ID    = org.doxygen.Publisher

# The DOCSET_PUBLISHER_NAME tag identifies the documentation publisher.
# The default value is: Publisher.
# This tag requires that the tag GENERATE_DOCSET is set to YES.

DOCSET_PUBLISHER_NAME  = Publisher

# If the GENERATE_HTMLHELP tag is set to YES then doxygen generates three
# additional HTML index files: index.hhp, index.hhc, and index.hhk. The
# index.hhp is a project file that can be read by Microsoft's HTML Help Workshop
# on Windows. In the beginning of 2021 Microsoft took the original page, with
# a.o. the download links, offline the HTML help workshop was already many years
# in maintenance mode). You can download the HTML help workshop from the web
# archives at Installation executable (see:
# http://web.archive.org/web/20160201063255/http://download.microsoft.com/downlo
# ad/0/A/9/0A939EF6-E31C-430F-A3DF-DFAE7960D564/htmlhelp.exe).
#
# The HTML Help Workshop contains a compiler that can convert all HTML output
# generated by doxygen into a single compiled HTML file (.chm). Compiled HTML
# files are now used as the Windows 98 help format, and will replace the old
# Windows help format (.hlp) on all Windows platforms in the future. Compressed
# HTML files also contain an index, a table of contents, and you can search for
# words in the documentation. The HTML workshop also contains a viewer for
# compressed HTML files.
# The default value is: NO.
# This tag requires that the tag GENERATE_HTML is set to YES.

GENERATE_HTMLHELP      = NO

# The CHM_FILE tag can be used to specify the file name of the resulting .chm
# file. You can add a path in front of the file if the result should not be
# written to the html output directory.
# This tag requires that the tag GENERATE_HTMLHELP is set to YES.

CHM_FILE               =

# The HHC_LOCATION tag can be used to specify the location (absolute path
# including file name) of the HTML help compiler (hhc.exe). If non-empty,
# doxygen will try to run the HTML help compiler on the generated index.hhp.
# The file has to be specified with full path.
# This tag requires that the tag GENERATE_HTMLHELP is set to YES.

HHC_LOCATION           =

# The GENERATE_CHI flag controls if a separate .chi index file is generated
# (YES) or that it should be included in the main .chm file (NO).
# The default value is: NO.
# This tag requires that the tag GENERATE_HTMLHELP is set to YES.

GENERATE_CHI           = NO

# The CHM_INDEX_ENCODING is used to encode HtmlHelp index (hhk), content (hhc)
# and project file content.
# This tag requires that the tag GENERATE_HTMLHELP is set to YES.

CHM_INDEX_ENCODING     =

# The BINARY_TOC flag controls whether a binary table of contents is generated
# (YES) or a normal table of contents (NO) in the .chm file. Furthermore it
# enables the Previous and Next buttons.
# The default value is: NO.
# This tag requires that the tag GENERATE_HTMLHELP is set to YES.

BINARY_TOC             = NO

# The TOC_EXPAND flag can be set to YES to add extra items for group members to
# the table of contents of the HTML help documentation and to the tree view.
# The default value is: NO.
# This tag requires that the tag GENERATE_HTMLHELP is set to YES.

TOC_EXPAND             = NO

# The SITEMAP_URL tag is used to specify the full URL of the place where the
# generated documentation will be placed on the server by the user during the
# deployment of the documentation. The generated sitemap is called sitemap.xml
# and placed on the directory specified by HTML_OUTPUT. In case no SITEMAP_URL
# is specified no sitemap is generated. For information about the sitemap
# protocol see https://www.sitemaps.org
# This tag requires that the tag GENERATE_HTML is set to YES.

SITEMAP_URL            =

# If the GENERATE_QHP tag is set to YES and both QHP_NAMESPACE and
# QHP_VIRTUAL_FOLDER are set, an additional index file will be generated that
# can be used as input for Qt's qhelpgenerator to generate a Qt Compressed Help
# (.qch) of the generated HTML documentation.
# The default value is: NO.
# This tag requires that the tag GENERATE_HTML is set to YES.

GENERATE_QHP           = NO

# If the QHG_LOCATION tag is specified, the QCH_FILE tag can be used to specify
# the file name of the resulting .qch file. The path specified is relative to
# the HTML output folder.
# This tag requires that the tag GENERATE_QHP is set to YES.

QCH_FILE               =

# The QHP_NAMESPACE tag specifies the namespace to use when generating Qt Help
# Project output. For more information please see Qt Help Project / Namespace
# (see:
# https://doc.qt.io/archives/qt-4.8/qthelpproject.html#namespace).
# The default value is: org.doxygen.Project.
# This tag requires that the tag GENERATE_QHP is set to YES.

QHP_NAMESPACE          = org.doxygen.Project

# The QHP_VIRTUAL_FOLDER tag specifies the namespace to use when generating Qt
# Help Project output. For more information please see Qt Help Project / Virtual
# Folders (see:
# https://doc.qt.io/archives/qt-4.8/qthelpproject.html#virtual-folders).
# The default value is: doc.
# This tag requires that the tag GENERATE_QHP is set to YES.

QHP_VIRTUAL_FOLDER     = doc

# If the QHP_CUST_FILTER_NAME tag is set, it specifies the name of a custom
# filter to add. For more information please see Qt Help Project / Custom
# Filters (see:
# https://doc.qt.io/archives/qt-4.8/qthelpproject.html#custom-filters).
# This tag requires that the tag GENERATE_QHP is set to YES.

QHP_CUST_FILTER_NAME   =

# The QHP_CUST_FILTER_ATTRS tag specifies the list of the attributes of the
# custom filter to add. For more information please see Qt Help Project / Custom
# Filters (see:
# https://doc.qt.io/archives/qt-4.8/qthelpproject.html#custom-filters).
# This tag requires that the tag GENERATE_QHP is set to YES.

QHP_CUST_FILTER_ATTRS  =

# The QHP_SECT_FILTER_ATTRS tag specifies the list of the attributes this
# project's filter section matches. Qt Help Project / Filter Attributes (see:
# https://doc.qt.io/archives/qt-4.8/qthelpproject.html#filter-attributes).
# This tag requires that the tag GENERATE_QHP is set to YES.

QHP_SECT_FILTER_ATTRS  =

# The QHG_LOCATION tag can be used to specify the location (absolute path
# including file name) of Qt's qhelpgenerator. If non-empty doxygen will try to
# run qhelpgenerator on the generated .qhp file.
# This tag requires that the tag GENERATE_QHP is set to YES.

QHG_LOCATION           =

# If the GENERATE_ECLIPSEHELP tag is set to YES, additional index files will be
# generated, together with the HTML files, they form an Eclipse help plugin. To
# install this plugin and make it available under the help contents menu in
# Eclipse, the contents of the directory containing the HTML and XML files needs
# to be copied into the plugins directory of eclipse. The name of the directory
# within the plugins directory should be the same as the ECLIPSE_DOC_ID value.
# After copying Eclipse needs to be restarted before the help appears.
# The default value is: NO.
# This tag requires that the tag GENERATE_HTML is set to YES.

GENERATE_ECLIPSEHELP   = NO

# A unique identifier for the Eclipse help plugin. When installing the plugin
# the directory name containing the HTML and XML files should also have this
# name. Each documentation set should have its own identifier.
# The default value is: org.doxygen.Project.
# This tag requires that the tag GENERATE_ECLIPSEHELP is set to YES.

ECLIPSE_DOC_ID         = org.doxygen.Project

# If you want full control over the layout of the generated HTML pages it might
# be necessary to disable the index and replace it with your own. The
# DISABLE_INDEX tag can be used to turn on/off the condensed index (tabs) at top
# of each HTML page. A value of NO enables the index and the value YES disables
# it. Since the tabs in the index contain the same information as the navigation
# tree, you can set this option to YES if you also set GENERATE_TREEVIEW to YES.
# The default value is: NO.
# This tag requires that the tag GENERATE_HTML is set to YES.

DISABLE_INDEX          = NO

# The GENERATE_TREEVIEW tag is used to specify whether a tree-like index
# structure should be generated to display hierarchical information. If the tag
# value is set to YES, a side panel will be generated containing a tree-like
# index structure (just like the one that is generated for HTML Help). For this
# to work a browser that supports JavaScript, DHTML, CSS and frames is required
# (i.e. any modern browser). Windows users are probably better off using the
# HTML help feature. Via custom style sheets (see HTML_EXTRA_STYLESHEET) one can
# further fine tune the look of the index (see "Fine-tuning the output"). As an
# example, the default style sheet generated by doxygen has an example that
# shows how to put an image at the root of the tree instead of the PROJECT_NAME.
# Since the tree basically has the same information as the tab index, you could
# consider setting DISABLE_INDEX to YES when enabling this option.
# The default value is: NO.
# This tag requires that the tag GENERATE_HTML is set to YES.

GENERATE_TREEVIEW      = YES

# When both GENERATE_TREEVIEW and DISABLE_INDEX are set to YES, then the
# FULL_SIDEBAR option determines if the side bar is limited to only the treeview
# area (value NO) or if it should extend to the full height of the window (value
# YES). Setting this to YES gives a layout similar to
# https://docs.readthedocs.io with more room for contents, but less room for the
# project logo, title, and description. If either GENERATE_TREEVIEW or
# DISABLE_INDEX is set to NO, this option has no effect.
# The default value is: NO.
# This tag requires that the tag GENERATE_HTML is set to YES.

FULL_SIDEBAR           = NO

# The ENUM_VALUES_PER_LINE tag can be used to set the number of enum values that
# doxygen will group on one line in the generated HTML documentation.
#
# Note that a value of 0 will completely suppress the enum values from appearing
# in the overview section.
# Minimum value: 0, maximum value: 20, default value: 4.
# This tag requires that the tag GENERATE_HTML is set to YES.

ENUM_VALUES_PER_LINE   = 4

# If the treeview is enabled (see GENERATE_TREEVIEW) then this tag can be used
# to set the initial width (in pixels) of the frame in which the tree is shown.
# Minimum value: 0, maximum value: 1500, default value: 250.
# This tag requires that the tag GENERATE_HTML is set to YES.

TREEVIEW_WIDTH         = 250

# If the EXT_LINKS_IN_WINDOW option is set to YES, doxygen will open links to
# external symbols imported via tag files in a separate window.
# The default value is: NO.
# This tag requires that the tag GENERATE_HTML is set to YES.

EXT_LINKS_IN_WINDOW    = NO

# If the OBFUSCATE_EMAILS tag is set to YES, doxygen will obfuscate email
# addresses.
# The default value is: YES.
# This tag requires that the tag GENERATE_HTML is set to YES.

OBFUSCATE_EMAILS       = YES

# If the HTML_FORMULA_FORMAT option is set to svg, doxygen will use the pdf2svg
# tool (see https://github.com/dawbarton/pdf2svg) or inkscape (see
# https://inkscape.org) to generate formulas as SVG images instead of PNGs for
# the HTML output. These images will generally look nicer at scaled resolutions.
# Possible values are: png (the default) and svg (looks nicer but requires the
# pdf2svg or inkscape tool).
# The default value is: png.
# This tag requires that the tag GENERATE_HTML is set to YES.

HTML_FORMULA_FORMAT    = png

# Use this tag to change the font size of LaTeX formulas included as images in
# the HTML documentation. When you change the font size after a successful
# doxygen run you need to manually remove any form_*.png images from the HTML
# output directory to force them to be regenerated.
# Minimum value: 8, maximum value: 50, default value: 10.
# This tag requires that the tag GENERATE_HTML is set to YES.

FORMULA_FONTSIZE       = 10

# The FORMULA_MACROFILE can contain LaTeX \newcommand and \renewcommand commands
# to create new LaTeX commands to be used in formulas as building blocks. See
# the section "Including formulas" for details.

FORMULA_MACROFILE      =

# Enable the USE_MATHJAX option to render LaTeX formulas using MathJax (see
# https://www.mathjax.org) which uses client side JavaScript for the rendering
# instead of using pre-rendered bitmaps. Use this if you do not have LaTeX
# installed or if you want to formulas look prettier in the HTML output. When
# enabled you may also need to install MathJax separately and configure the path
# to it using the MATHJAX_RELPATH option.
# The default value is: NO.
# This tag requires that the tag GENERATE_HTML is set to YES.

USE_MATHJAX            = NO

# With MATHJAX_VERSION it is possible to specify the MathJax version to be used.
# Note that the different versions of MathJax have different requirements with
# regards to the different settings, so it is possible that also other MathJax
# settings have to be changed when switching between the different MathJax
# versions.
# Possible values are: MathJax_2 and MathJax_3.
# The default value is: MathJax_2.
# This tag requires that the tag USE_MATHJAX is set to YES.

MATHJAX_VERSION        = MathJax_2

# When MathJax is enabled you can set the default output format to be used for
# the MathJax output. For more details about the output format see MathJax
# version 2 (see:
# http://docs.mathjax.org/en/v2.7-latest/output.html) and MathJax version 3
# (see:
# http://docs.mathjax.org/en/latest/web/components/output.html).
# Possible values are: HTML-CSS (which is slower, but has the best
# compatibility. This is the name for Mathjax version 2, for MathJax version 3
# this will be translated into chtml), NativeMML (i.e. MathML. Only supported
# for NathJax 2. For MathJax version 3 chtml will be used instead.), chtml (This
# is the name for Mathjax version 3, for MathJax version 2 this will be
# translated into HTML-CSS) and SVG.
# The default value is: HTML-CSS.
# This tag requires that the tag USE_MATHJAX is set to YES.

MATHJAX_FORMAT         = HTML-CSS

# When MathJax is enabled you need to specify the location relative to the HTML
# output directory using the MATHJAX_RELPATH option. The destination directory
# should contain the MathJax.js script. For instance, if the mathjax directory
# is located at the same level as the HTML output directory, then
# MATHJAX_RELPATH should be ../mathjax. The default value points to the MathJax
# Content Delivery Network so you can quickly see the result without installing
# MathJax. However, it is strongly recommended to install a local copy of
# MathJax from https://www.mathjax.org before deployment. The default value is:
# - in case of MathJax version 2: https://cdn.jsdelivr.net/npm/mathjax@2
# - in case of MathJax version 3: https://cdn.jsdelivr.net/npm/mathjax@3
# This tag requires that the tag USE_MATHJAX is set to YES.

MATHJAX_RELPATH        =

# The MATHJAX_EXTENSIONS tag can be used to specify one or more MathJax
# extension names that should be enabled during MathJax rendering. For example
# for MathJax version 2 (see
# https://docs.mathjax.org/en/v2.7-latest/tex.html#tex-and-latex-extensions):
# MATHJAX_EXTENSIONS = TeX/AMSmath TeX/AMSsymbols
# For example for MathJax version 3 (see
# http://docs.mathjax.org/en/latest/input/tex/extensions/index.html):
# MATHJAX_EXTENSIONS = ams
# This tag requires that the tag USE_MATHJAX is set to YES.

MATHJAX_EXTENSIONS     =

# The MATHJAX_CODEFILE tag can be used to specify a file with javascript pieces
# of code that will be used on startup of the MathJax code. See the MathJax site
# (see:
# http://docs.mathjax.org/en/v2.7-latest/output.html) for more details. For an
# example see the documentation.
# This tag requires that the tag USE_MATHJAX is set to YES.

MATHJAX_CODEFILE       =

# When the SEARCHENGINE tag is enabled doxygen will generate a search box for
# the HTML output. The underlying search engine uses javascript and DHTML and
# should work on any modern browser. Note that when using HTML help
# (GENERATE_HTMLHELP), Qt help (GENERATE_QHP), or docsets (GENERATE_DOCSET)
# there is already a search function so this one should typically be disabled.
# For large projects the javascript based search engine can be slow, then
# enabling SERVER_BASED_SEARCH may provide a better solution. It is possible to
# search using the keyboard; to jump to the search box use <access key> + S
# (what the <access key> is depends on the OS and browser, but it is typically
# <CTRL>, <ALT>/<option>, or both). Inside the search box use the <cursor down
# key> to jump into the search results window, the results can be navigated
# using the <cursor keys>. Press <Enter> to select an item or <escape> to cancel
# the search. The filter options can be selected when the cursor is inside the
# search box by pressing <Shift>+<cursor down>. Also here use the <cursor keys>
# to select a filter and <Enter> or <escape> to activate or cancel the filter
# option.
# The default value is: YES.
# This tag requires that the tag GENERATE_HTML is set to YES.

SEARCHENGINE           = YES

# When the SERVER_BASED_SEARCH tag is enabled the search engine will be
# implemented using a web server instead of a web client using JavaScript. There
# are two flavors of web server based searching depending on the EXTERNAL_SEARCH
# setting. When disabled, doxygen will generate a PHP script for searching and
# an index file used by the script. When EXTERNAL_SEARCH is enabled the indexing
# and searching needs to be provided by external tools. See the section
# "External Indexing and Searching" for details.
# The default value is: NO.
# This tag requires that the tag SEARCHENGINE is set to YES.

SERVER_BASED_SEARCH    = NO

# When EXTERNAL_SEARCH tag is enabled doxygen will no longer generate the PHP
# script for searching. Instead the search results are written to an XML file
# which needs to be processed by an external indexer. Doxygen will invoke an
# external search engine pointed to by the SEARCHENGINE_URL option to obtain the
# search results.
#
# Doxygen ships with an example indexer (doxyindexer) and search engine
# (doxysearch.cgi) which are based on the open source search engine library
# Xapian (see:
# https://xapian.org/).
#
# See the section "External Indexing and Searching" for details.
# The default value is: NO.
# This tag requires that the tag SEARCHENGINE is set to YES.

EXTERNAL_SEARCH        = NO

# The SEARCHENGINE_URL should point to a search engine hosted by a web server
# which will return the search results when EXTERNAL_SEARCH is enabled.
#
# Doxygen ships with an example indexer (doxyindexer) and search engine
# (doxysearch.cgi) which are based on the open source search engine library
# Xapian (see:
# https://xapian.org/). See the section "External Indexing and Searching" for
# details.
# This tag requires that the tag SEARCHENGINE is set to YES.

SEARCHENGINE_URL       =

# When SERVER_BASED_SEARCH and EXTERNAL_SEARCH are both enabled the unindexed
# search data is written to a file for indexing by an external tool. With the
# SEARCHDATA_FILE tag the name of this file can be specified.
# The default file is: searchdata.xml.
# This tag requires that the tag SEARCHENGINE is set to YES.

SEARCHDATA_FILE        = searchdata.xml

# When SERVER_BASED_SEARCH and EXTERNAL_SEARCH are both enabled the
# EXTERNAL_SEARCH_ID tag can be used as an identifier for the project. This is
# useful in combination with EXTRA_SEARCH_MAPPINGS to search through multiple
# projects and redirect the results back to the right project.
# This tag requires that the tag SEARCHENGINE is set to YES.

EXTERNAL_SEARCH_ID     =

# The EXTRA_SEARCH_MAPPINGS tag can be used to enable searching through doxygen
# projects other than the one defined by this configuration file, but that are
# all added to the same external search index. Each project needs to have a
# unique id set via EXTERNAL_SEARCH_ID. The search mapping then maps the id of
# to a relative location where the documentation can be found. The format is:
# EXTRA_SEARCH_MAPPINGS = tagname1=loc1 tagname2=loc2 ...
# This tag requires that the tag SEARCHENGINE is set to YES.

EXTRA_SEARCH_MAPPINGS  =

#---------------------------------------------------------------------------
# Configuration options related to the LaTeX output
#---------------------------------------------------------------------------

# If the GENERATE_LATEX tag is set to YES, doxygen will generate LaTeX output.
# The default value is: YES.

GENERATE_LATEX         = NO

# The LATEX_OUTPUT tag is used to specify where the LaTeX docs will be put. If a
# relative path is entered the value of OUTPUT_DIRECTORY will be put in front of
# it.
# The default directory is: latex.
# This tag requires that the tag GENERATE_LATEX is set to YES.

LATEX_OUTPUT           = latex

# The LATEX_CMD_NAME tag can be used to specify the LaTeX command name to be
# invoked.
#
# Note that when not enabling USE_PDFLATEX the default is latex when enabling
# USE_PDFLATEX the default is pdflatex and when in the later case latex is
# chosen this is overwritten by pdflatex. For specific output languages the
# default can have been set differently, this depends on the implementation of
# the output language.
# This tag requires that the tag GENERATE_LATEX is set to YES.

LATEX_CMD_NAME         =

# The MAKEINDEX_CMD_NAME tag can be used to specify the command name to generate
# index for LaTeX.
# Note: This tag is used in the Makefile / make.bat.
# See also: LATEX_MAKEINDEX_CMD for the part in the generated output file
# (.tex).
# The default file is: makeindex.
# This tag requires that the tag GENERATE_LATEX is set to YES.

MAKEINDEX_CMD_NAME     = makeindex

# The LATEX_MAKEINDEX_CMD tag can be used to specify the command name to
# generate index for LaTeX. In case there is no backslash (\) as first character
# it will be automatically added in the LaTeX code.
# Note: This tag is used in the generated output file (.tex).
# See also: MAKEINDEX_CMD_NAME for the part in the Makefile / make.bat.
# The default value is: makeindex.
# This tag requires that the tag GENERATE_LATEX is set to YES.

LATEX_MAKEINDEX_CMD    = makeindex

# If the COMPACT_LATEX tag is set to YES, doxygen generates more compact LaTeX
# documents. This may be useful for small projects and may help to save some
# trees in general.
# The default value is: NO.
# This tag requires that the tag GENERATE_LATEX is set to YES.

COMPACT_LATEX          = NO

# The PAPER_TYPE tag can be used to set the paper type that is used by the
# printer.
# Possible values are: a4 (210 x 297 mm), letter (8.5 x 11 inches), legal (8.5 x
# 14 inches) and executive (7.25 x 10.5 inches).
# The default value is: a4.
# This tag requires that the tag GENERATE_LATEX is set to YES.

PAPER_TYPE             = a4

# The EXTRA_PACKAGES tag can be used to specify one or more LaTeX package names
# that should be included in the LaTeX output. The package can be specified just
# by its name or with the correct syntax as to be used with the LaTeX
# \usepackage command. To get the times font for instance you can specify :
# EXTRA_PACKAGES=times or EXTRA_PACKAGES={times}
# To use the option intlimits with the amsmath package you can specify:
# EXTRA_PACKAGES=[intlimits]{amsmath}
# If left blank no extra packages will be included.
# This tag requires that the tag GENERATE_LATEX is set to YES.

EXTRA_PACKAGES         =

# The LATEX_HEADER tag can be used to specify a user-defined LaTeX header for
# the generated LaTeX document. The header should contain everything until the
# first chapter. If it is left blank doxygen will generate a standard header. It
# is highly recommended to start with a default header using
# doxygen -w latex new_header.tex new_footer.tex new_stylesheet.sty
# and then modify the file new_header.tex. See also section "Doxygen usage" for
# information on how to generate the default header that doxygen normally uses.
#
# Note: Only use a user-defined header if you know what you are doing!
# Note: The header is subject to change so you typically have to regenerate the
# default header when upgrading to a newer version of doxygen. The following
# commands have a special meaning inside the header (and footer): For a
# description of the possible markers and block names see the documentation.
# This tag requires that the tag GENERATE_LATEX is set to YES.

LATEX_HEADER           =

# The LATEX_FOOTER tag can be used to specify a user-defined LaTeX footer for
# the generated LaTeX document. The footer should contain everything after the
# last chapter. If it is left blank doxygen will generate a standard footer. See
# LATEX_HEADER for more information on how to generate a default footer and what
# special commands can be used inside the footer. See also section "Doxygen
# usage" for information on how to generate the default footer that doxygen
# normally uses. Note: Only use a user-defined footer if you know what you are
# doing!
# This tag requires that the tag GENERATE_LATEX is set to YES.

LATEX_FOOTER           =

# The LATEX_EXTRA_STYLESHEET tag can be used to specify additional user-defined
# LaTeX style sheets that are included after the standard style sheets created
# by doxygen. Using this option one can overrule certain style aspects. Doxygen
# will copy the style sheet files to the output directory.
# Note: The order of the extra style sheet files is of importance (e.g. the last
# style sheet in the list overrules the setting of the previous ones in the
# list).
# This tag requires that the tag GENERATE_LATEX is set to YES.

LATEX_EXTRA_STYLESHEET =

# The LATEX_EXTRA_FILES tag can be used to specify one or more extra images or
# other source files which should be copied to the LATEX_OUTPUT output
# directory. Note that the files will be copied as-is; there are no commands or
# markers available.
# This tag requires that the tag GENERATE_LATEX is set to YES.

LATEX_EXTRA_FILES      =

# If the PDF_HYPERLINKS tag is set to YES, the LaTeX that is generated is
# prepared for conversion to PDF (using ps2pdf or pdflatex). The PDF file will
# contain links (just like the HTML output) instead of page references. This
# makes the output suitable for online browsing using a PDF viewer.
# The default value is: YES.
# This tag requires that the tag GENERATE_LATEX is set to YES.

PDF_HYPERLINKS         = YES

# If the USE_PDFLATEX tag is set to YES, doxygen will use the engine as
# specified with LATEX_CMD_NAME to generate the PDF file directly from the LaTeX
# files. Set this option to YES, to get a higher quality PDF documentation.
#
# See also section LATEX_CMD_NAME for selecting the engine.
# The default value is: YES.
# This tag requires that the tag GENERATE_LATEX is set to YES.

USE_PDFLATEX           = YES

# The LATEX_BATCHMODE tag ignals the behavior of LaTeX in case of an error.
# Possible values are: NO same as ERROR_STOP, YES same as BATCH, BATCH In batch
# mode nothing is printed on the terminal, errors are scrolled as if <return> is
# hit at every error; missing files that TeX tries to input or request from
# keyboard input (\read on a not open input stream) cause the job to abort,
# NON_STOP In nonstop mode the diagnostic message will appear on the terminal,
# but there is no possibility of user interaction just like in batch mode,
# SCROLL In scroll mode, TeX will stop only for missing files to input or if
# keyboard input is necessary and ERROR_STOP In errorstop mode, TeX will stop at
# each error, asking for user intervention.
# The default value is: NO.
# This tag requires that the tag GENERATE_LATEX is set to YES.

LATEX_BATCHMODE        = NO

# If the LATEX_HIDE_INDICES tag is set to YES then doxygen will not include the
# index chapters (such as File Index, Compound Index, etc.) in the output.
# The default value is: NO.
# This tag requires that the tag GENERATE_LATEX is set to YES.

LATEX_HIDE_INDICES     = NO

# The LATEX_BIB_STYLE tag can be used to specify the style to use for the
# bibliography, e.g. plainnat, or ieeetr. See
# https://en.wikipedia.org/wiki/BibTeX and \cite for more info.
# The default value is: plain.
# This tag requires that the tag GENERATE_LATEX is set to YES.

LATEX_BIB_STYLE        = plain

# The LATEX_EMOJI_DIRECTORY tag is used to specify the (relative or absolute)
# path from which the emoji images will be read. If a relative path is entered,
# it will be relative to the LATEX_OUTPUT directory. If left blank the
# LATEX_OUTPUT directory will be used.
# This tag requires that the tag GENERATE_LATEX is set to YES.

LATEX_EMOJI_DIRECTORY  =

#---------------------------------------------------------------------------
# Configuration options related to the RTF output
#---------------------------------------------------------------------------

# If the GENERATE_RTF tag is set to YES, doxygen will generate RTF output. The
# RTF output is optimized for Word 97 and may not look too pretty with other RTF
# readers/editors.
# The default value is: NO.

GENERATE_RTF           = NO

# The RTF_OUTPUT tag is used to specify where the RTF docs will be put. If a
# relative path is entered the value of OUTPUT_DIRECTORY will be put in front of
# it.
# The default directory is: rtf.
# This tag requires that the tag GENERATE_RTF is set to YES.

RTF_OUTPUT             = rtf

# If the COMPACT_RTF tag is set to YES, doxygen generates more compact RTF
# documents. This may be useful for small projects and may help to save some
# trees in general.
# The default value is: NO.
# This tag requires that the tag GENERATE_RTF is set to YES.

COMPACT_RTF            = NO

# If the RTF_HYPERLINKS tag is set to YES, the RTF that is generated will
# contain hyperlink fields. The RTF file will contain links (just like the HTML
# output) instead of page references. This makes the output suitable for online
# browsing using Word or some other Word compatible readers that support those
# fields.
#
# Note: WordPad (write) and others do not support links.
# The default value is: NO.
# This tag requires that the tag GENERATE_RTF is set to YES.

RTF_HYPERLINKS         = NO

# Load stylesheet definitions from file. Syntax is similar to doxygen's
# configuration file, i.e. a series of assignments. You only have to provide
# replacements, missing definitions are set to their default value.
#
# See also section "Doxygen usage" for information on how to generate the
# default style sheet that doxygen normally uses.
# This tag requires that the tag GENERATE_RTF is set to YES.

RTF_STYLESHEET_FILE    =

# Set optional variables used in the generation of an RTF document. Syntax is
# similar to doxygen's configuration file. A template extensions file can be
# generated using doxygen -e rtf extensionFile.
# This tag requires that the tag GENERATE_RTF is set to YES.

RTF_EXTENSIONS_FILE    =

#---------------------------------------------------------------------------
# Configuration options related to the man page output
#---------------------------------------------------------------------------

# If the GENERATE_MAN tag is set to YES, doxygen will generate man pages for
# classes and files.
# The default value is: NO.

GENERATE_MAN           = NO

# The MAN_OUTPUT tag is used to specify where the man pages will be put. If a
# relative path is entered the value of OUTPUT_DIRECTORY will be put in front of
# it. A directory man3 will be created inside the directory specified by
# MAN_OUTPUT.
# The default directory is: man.
# This tag requires that the tag GENERATE_MAN is set to YES.

MAN_OUTPUT             = man
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

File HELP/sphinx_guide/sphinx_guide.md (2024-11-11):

# Sphinx Guide
Sphinx is a tool to automate documentation for Python software.

## Let's Use Sphinx
There isn't much- you just pip install Sphinx, put together a couple of configuration files, and let it rip.

- Install Sphinx: `pip install sphinx`
- Create a "docs" folder to contain all Sphinx configuration and build files
- Create configuration files:
  - **conf.py**
    - Configures HTML files generated
    - Make sure that the path in `os.path.abspath()` leads to your source files
    - Example of conf.py file:
```python
# docs/conf.py

import os
import sys

# Include the root directory in the Python path
sys.path.insert(0, os.path.abspath('../../../source'))  # Include the root directory in the Python path

# Project Information
project = 'Project Name Here'
author = 'Team Name Here'
version = '1.0'
release = '1.0.0'

# General Configuration
extensions = [
    'sphinx.ext.autodoc',   # Auto-generate documentation from docstrings
    'sphinx.ext.napoleon',  # Support for Google-style and NumPy-style docstrings
    'sphinx.ext.viewcode',  # Include links to the source code
]
templates_path = ['_templates']  # Path to custom templates
exclude_patterns = []            # Exclude certain files/folders from documentation

# HTML Output Configuration
html_theme = 'bizstyle'  # You can choose other themes like 'sphinx_rtd_theme'
#html_static_path = ['_static']  # Path to custom static files (CSS, JavaScript)
```

  - **index.rst**
    - Configures Index page that's generated
    - Example of index.rst file:
```
.. My Project documentation master file

Project Name Here
======================================

.. toctree::
   :maxdepth: 1
   :caption: Contents:

   module_name_here
```
  - **xxx.rst** 
    - You need to create a ReStructured Text (rst) markup file for every Python file (aka module)
    - This can be automated by using Sphinx: `sphinx-apidoc -o <output_directory> <input_directory>` 
    - Example of Python module rst file:
```
module_name_here
===================

.. automodule:: module_name_here
   :members:
   :undoc-members:
   :show-inheritance:
```

- w/ cmd in the docs directory run `sphinx-build -b html docs/ docs/_build`
- go into the build folder and double click on the index.html file to open the generated documentation

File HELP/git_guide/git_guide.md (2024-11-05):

# Git Guide (bare-minimum)
Git is a must-have tool to manage project history and collaborate w/ others. It seems overwheling at first, but there's **very little you need to know** to use Git for its basic purpose. 
- This guide:
    - Assumes Git Bash command line
    - Doesn't cover merge conflicts or rebasing- avoid overlap in work allocation if possible...
    - Uses merge requests & conventional commit messages for good practice

## Index
- **Essentials**
  - [Let's Use Git](#)
  - [Using Git Flowchart](#using-git-flowchart)
  - [Conventional Git Commit Messages](#conventional-git-commit-messages)

- **References and Details**
  - [Important Git Commands](#details-important-git-commands)
  - [Git Jargon](#details-git-jargon)

## Let's Use Git
We want a single working copy of our project online on GitHub/GitLab, let everyone work on different parts of the project at the same time, and track every change that's made on the project. Here's the bare minimum we have to do:

**Initialization**:
- Install Git Bash (and log into GitLab account or create a GitHub account)
- Navigate Git Bash to the directory where you want your project to be (`cd <your_project_path>`)
- If you're contributing to an existing GitHub/GitLab remote repo
  - clone the remote repo using `git clone <project_url>` ->
- If you're making a completely new project
  - Start a new repo via `git init <new_project_directory_name>` ->
  - Create a new project on GitHub/GitLab and get the project URL
    - Make sure to uncheck "Initialize repository with a README" (having this checked will force you to use `git push -f origin <branch_name_w_changes>` to forcefully push your Initial commit and overwrite the initial commit w/ the dummy README)
  - Link the local repo and remote repo w/ `git remote add origin <project_url>` ->
- Switch main branch name to “main” if it’s currently “master”
  - If remote repo works w/ “master” then it’s fine, but if the project is brand new: 
    - Confirm you’re on master branch (`git branch`) ->
    - `git branch -M main` to rename master to main
  - Skipping this step and trying to push changes and renaming the branch later will lead to weird issues- make sure to rename local branch name if needed

**Work Cycle**:
- Create a new branch or switch branches to start making project changes: 
  - `git checkout -b <new_branch_name>` to make a new branch to start making changes
  - `git checkout <branch_name>` or `git switch <branch_name>` if there's already a branch for you to make changes on
- Make changes on the new branch as needed ->
- `git add` to the staging area ->
- `git commit -m“type: subject”` to bundle related changes together: refer to [Conventional Git Commit Messages](#conventional-git-commit-messages) for commit message convention ->
- `git push -u origin <branch_name_w_changes>` to push new branch and associated changes to remote repo
- Repeat above until all changes are done
  - Group relevant changes together into commits
  - Don't stockpile too many unrelated commits into a single merge request
  - Renaming/moving files can be tracked as well- it can be its own commit and merge request
- **Create a Merge Request**:
    - Go to the remote repo on GitHub/GitLab and navigate to the new branch- you'll see your commit and push 
    - Click on "create merge request"
    - Customize the merge request if needed, and create the merge request
    - Review the merge request w/ your team members
    - if the merge request was accepted and the branch was deleted
      - `git fetch --prune` to update local repo w/ the branch deletion 
      - `git branch -d <branch to delete>` to delete the branch locally
      - Confirm that branches were deleted:
        - `git branch`
        - `git branch -r`
- After you're done w/ your changes, make sure to update your local repo w/ your team members' changes: 
  - switch to the main branch w/ `git switch main` if not already on main branch
  - `git fetch` and `git merge` to update local repository w/ others' changes

That's it! Everything you need to know (for now) fits in a page.

Merge conflicts and reverting things gets complicated, so try to allocate work so that team members are working on independent parts of the project.

## Using Git Flowchart
Below is a visual for using Git. 

You do the green stuff once, and continuously repeat the yellow stuff as you work. It's just a handful of commands you need to know on the regular.

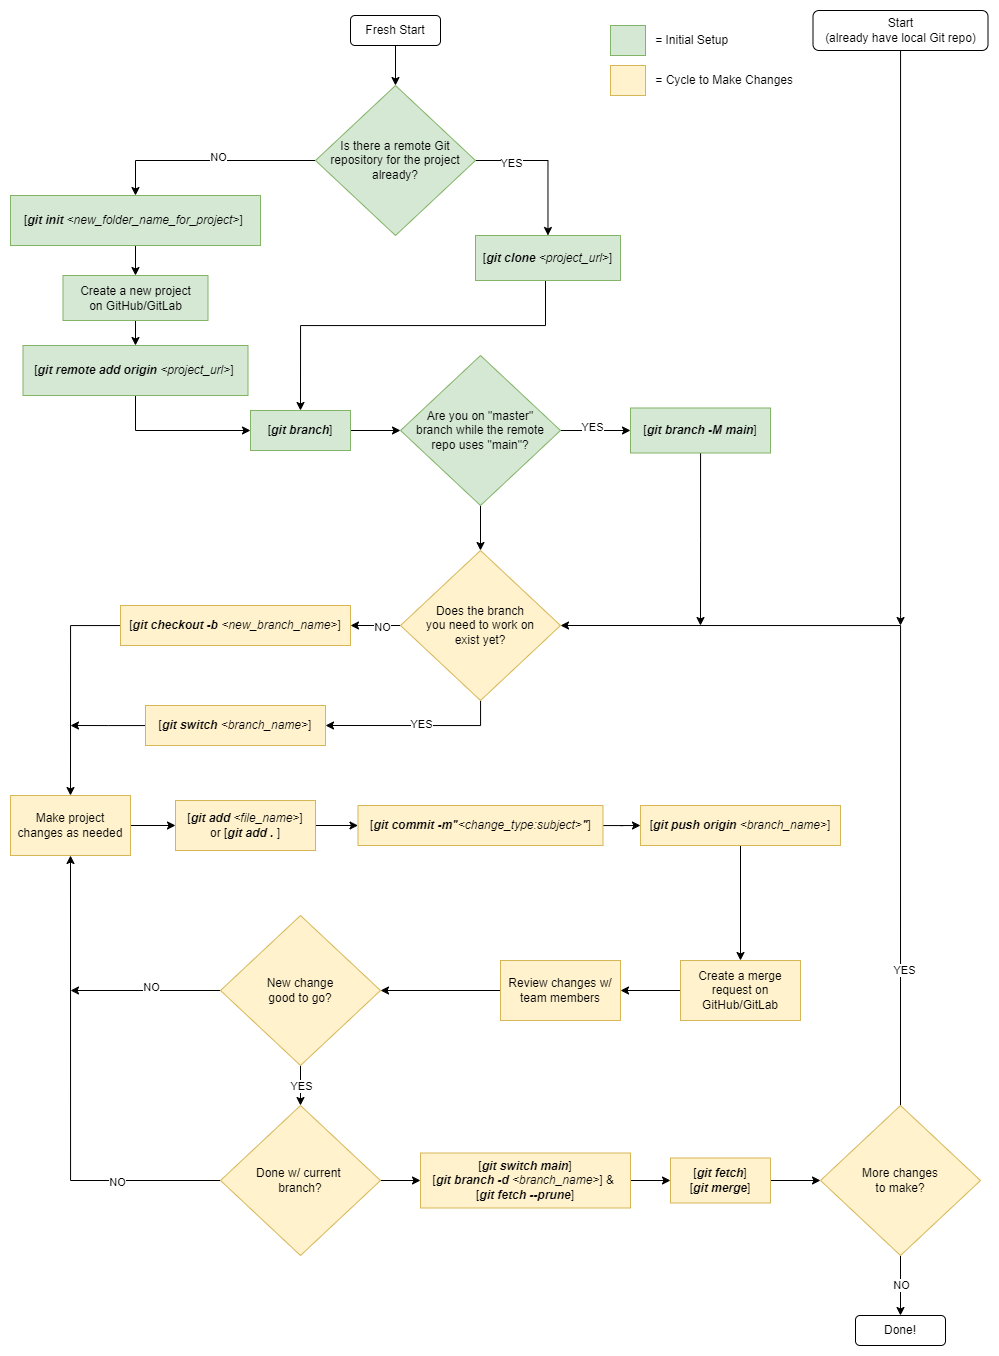
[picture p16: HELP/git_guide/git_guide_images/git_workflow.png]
Git Workflow


## Conventional Git Commit Messages
- To commit w/ a header, body, and footer the command is:
  - `git commit -m “<header>” -m “<body>” -m “<footer>`
- **Header**
  - `<type>(<scope>): <subject>`
  - Ex: `git commit -m“docs(changelog): update changelog to beta.5”`
  - `type`:
      - Must follow below convention to tie w/ *Semantic Versioning*:
        - fix
          - a commit of the type fix patches a bug in your codebase (this correlates with PATCH in Semantic Versioning).
        - feat
          - a commit of the type feat introduces a new feature to the codebase (this correlates with MINOR in Semantic Versioning).
        - BREAKING CHANGE
            - a commit that has a footer BREAKING CHANGE:, or appends a ! after the type/scope, introduces a breaking API change (correlating with MAJOR in Semantic Versioning). A BREAKING CHANGE can be part of commits of any type.
      - **Semantic Versioning**
        - There’s a standard for versioning software (Minecraft’s 1.7.2 wasn’t just some random numbers)
        - The format is Major.Minor.Patch
          - Major
            - Change require user to modify their code/configurations to work w/ new version
            - Fundamentally changes how software works
          - Minor
            - Backward compatible update that adds new features, enhancements, improvements without breaking existing functionality
            - Deprecate a feature but leave it available
            - Minor improvements that don’t require changes from user
          - Patch
            - Backward compatible bug fixes and small improvements that don’t add any new features

  - Possible types include:
    - **fix**
        - bug fix
    - **feat**
        - new feature
    - **build**
      - changes that affect the build system or external dependencies (example scopes: gulp, broccoli, npm)
    - **ci**
      - changes to our CI configuration files and scripts (example scopes: Travis, Circle, BrowserStack, SauceLabs)
    - **docs**
        - documentation only changes
    - **perf**
        - code change that improves performance
    - **refactor**
        - code change that neither fixes a bug nor adds a feature
    - **style**
        - changes that do not affect the meaning of the code (white-space, formatting, missing semi-colons, etc)
    - **test**
         - adding missing tests or correcting existing tests
  - `scope`
    - optional 
    - affected “packages” if there’s a clear scope affected by changes in commit
  - `subject`
    - short description of the change
    - use the imperative, present tense: "change" not "changed" nor "changes"
    - don't capitalize the first letter
    - no dot (.) at the end

- **Body**
  - Just as in the subject, use the imperative, present tense: "change" not "changed" nor "changes". The body should include the motivation for the change and contrast this with previous behavior.
- **Footer**
  - The footer should contain any information about Breaking Changes and is also the place to reference GitHub issues that this commit Closes.
  - Breaking Changes should start with the word “BREAKING CHANGE”: with a space or two newlines. The rest of the commit message is then used for this.

## Details: Git Jargon
Below are Git / version control words that are tossed around:
- Remote repo
  - online repository where working project files are stored and version controlled 
- Working directory / local repo
  - local directory / repository where project files are being modified (on your laptop/PC)
- Staging area
  - where files are stored when you use `git add <files>`
  - space to indicate the modified files that should be packaged into a commit to eventually update the project on the remote repository
  - allows preparation for a commit and eventual push to avoid constantly committing / uncommitting and fighting version history
- Branching
  - method to create a new line of development on a project
  - essential to keep the central repository clean and isolated from each development effort
- Main vs master
  - confusing- it's just the name of the main branch of central repository
  - GitHub goes w/ “main” now by default, but GitLab and raw Git still goes by “master” 
  - it’s just like the effort to change slave/master to client/host, follower/leader, etc
- Head
  - reference to a commit object- the commit in a branch that’s being worked on or viewed in particular
  - when head isn’t pointing to the latest commit (via “git checkout”), the head is “detached”
- Merge request
  - After committing changes to the central repo, you can make a “merge request” before changes are reflected on central repo
  - good to enforce code reviews and record all branch history
- Conventional commits
  - There’s a standard for how to make commit/revision messages
  - Link: https://www.conventionalcommits.org/en/v1.0.0/
  - w/ conventional commits we are barbarians no more
  - allows for easy navigation through Git commit history
- PAT
  - “personalized access token”
   - used to allow users access to API’s, command-line tools, and other automated systems on a version control system
- Merge conflict
  - occurs when you try to merge changes on local repository to central repo, but the central repo has changes on the same files that local repo has changes in
  - must be resolved w/ teammates before any further work
- .gitignore
  - file to specify files that shouldn’t be version controlled
- Fork
  - forking allows you to copy a repo from one Git account to another
- Rebasing
  - “git rebase”
  - method to combine commit history of one branch w/ another branch 
  - useful to avoid merge conflicts 

## Details: Important Git Commands
- `git --version` 
  - check if git installed
- `git init <new_project_directory_name>`
  - **don’t use this command inside of a repo**- that's what submodules are for
  - initializes git repo on local machine
  - creates .git file to manage versioning and history
  - creates a new directory in the directory wherever the cmd /Git Bash currently is w/ the provided directory name
 - `git remote add origin <repo-url>`
    - used to manage how a repository interacts w/ other repositories
    - not often used, but confused w/ `git clone`
    - If local repo created first before remote repo: after creating a remote repo on Gitlab/Github you can link a local repo to the remote repo w/ this command
 - `git clone <project url>`
    - used to copy a remote repository to your local machine if there’s a remote repo for a project already
 - `git status`
    - reports status of Git repo
    - essential- use it often to check Git status (status of commits, staged files, etc)
 - `git log`
    - shows list of commits made to repository
    - includes hash, message, metadata
 - `git branch`
    - displays branches being worked on 
    - `git branch <branch name>` creates a new branch
    - `git switch `switches branches
    - rename a branch
      - `git switch <branch to rename>`, and then `git branch -m <new branch name>`
    - delete branch
      - `git branch -d <branch to delete>`
      - branch currently being viewed (where head is pointing) can’t be deleted
      - you’ll get warned if your branch hasn’t merged w/ central repo yet
  - `git switch <branchname>`
      - switches to new branch
      - `git switch -c <branchname>` creates a new branch if there isn’t a branch named <branchname>
  - `git fetch`
      -  grabs changes in .git directory in remote central repository to prepare to update local repository
      - doesn’t update local repository yet
  - `git merge`
      - used to update local repository when central repo is ahead
      - also used to update central repo if local repo is ahead and no changes were made to central repo otherwise- **use merge requests instead** if you're trying to update the central repo
      - called “fast forward merge”
      - `git switch master`, and then `git merge <branch w/ changes>`
  - `git pull`
      - bad practice- don’t use unless you know it's a fetch & merge
      - updates local repository w/ files fetched w/ `git fetch`
      - same as running `git fetch` and then `git merge` 
      - `git fetch` and then `git merge` gives you better control of the process by showing you what's being fetched from the remote repository before you update your local repository
- `git diff`
  - displays differences between file and branch versions
  - `git diff <branch1> <branch2>`
- `git add <filename>` or `git add . `
  - add new or changed files to the staging area to prepare for a commit
- `git commit`
  - wrap together all desired changes on the staging area to be pushed to the remote repository w/ a commit message
  - refer to **“conventional commit messages”** to follow best commit practices
- `git push -xx origin <branch name>`
  - Push all commits prepared to central (master/main) repository 
  - `git push -u origin <main/master>`
  - Pushes commits to main/master branch called “origin”
  - The -u flag “sets the upstream branch”, meaning that local main branch is tied to remote origin/main branch so that future `git push` and `git pull` will default to this branch specified going forward
  - A -f flag forces the push to overwrite the remote branch w/ local branch ignoring conflicts and changes on remote branch that aren’t on local branch (overwrites remote history w/ local history)

__Undoing changes__
- `git rm --cached <filename>`
  - Remove file from staging area
- `git checkout`
  - Switching branches
      - `git checkout -b <branchname>`
      - Used to switch branches
      - The “-b” flag indicates that a new branch should be created if it doesn’t exist
      - Later comes along `git switch <branchname>` and `git switch -c <branchname>` to switch branches and create new branches, but `git checkout` can do this too
  - Switch to old revision:
      - Switching to old revision of a branch
      - `git checkout <7 digit rev # found w/ git log>` 
      - Commits can’t be made while head is “detached”, but you can make a new branch while the head is detached to then make changes and eventually merge to central repo
- `git restore`
    - Restores a file back to most latest commit
    - Changes that weren’t committed CAN’T be recovered
    - `git restore <filename>`
    - `git restore –source HEAD~<N> <filename>`
    - N is number of commits behind latest commit if we want to go back further
- `git reset`
    - Deletes commits/revisions 
    - `git reset <7 digit rev #>`
      - Moves head pointer to specific rev #
      - Doesn’t change local directory files or staging area
    - `git reset <7 digit rev #> --hard` 
      - Moves head pointer to specific rev #, and modifies local directory to match rev # and clears out staging area
- `git revert` 
    - Undoes work from a particular commit/rev, but doesn’t delete the commit/rev from history
    - Preferred over `git reset` to preserve history
- `git stash`
    - Allows context switching (switching between branches) while you have changes for a particular branch
    - `git stash pop` unstashes the changes to be applied

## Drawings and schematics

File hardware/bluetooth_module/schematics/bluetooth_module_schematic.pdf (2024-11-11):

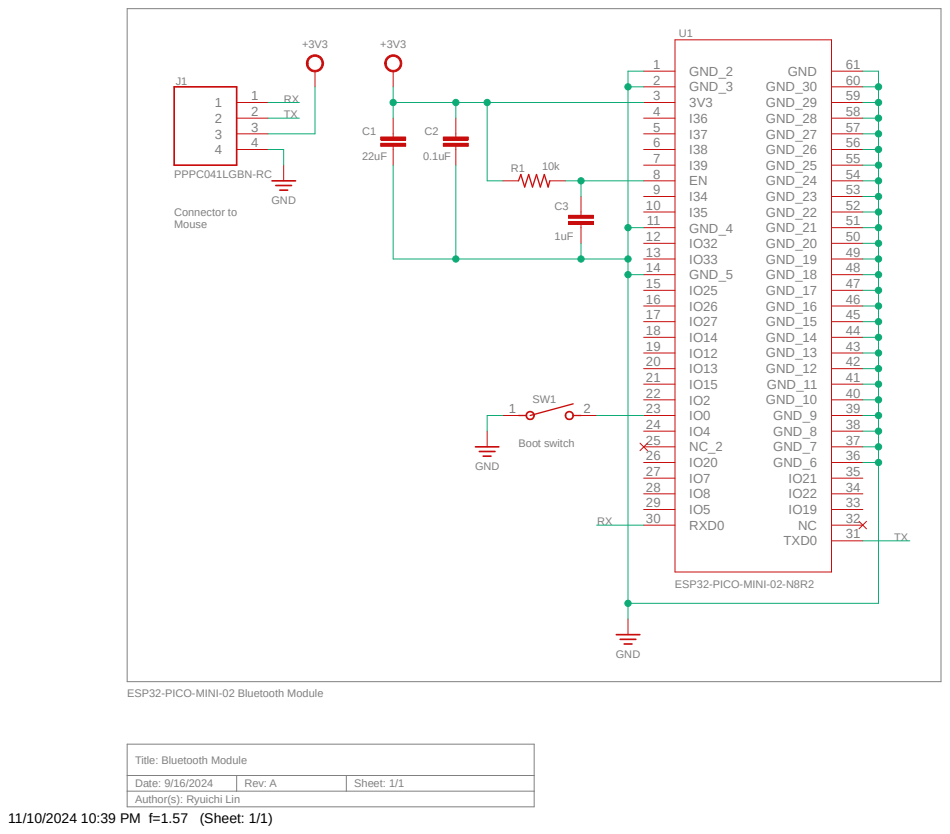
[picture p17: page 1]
11/10/2024 10:39 PM f=1.57 (Sheet: 1/1); Date: 9/16/2024; Rev: A; Sheet: 1/1; Connector to Mouse; Boot switch; PPPC041LGBN-RC; ESP32-PICO-MINI-02-N8R2; GND; GND_2 1 GND_3 2 3V3 3 I36 4 I37 5 I38 6 I39 7 EN 8 I34 9 I35 10 GND_4 11 IO32 12 IO33 13 GND_5 14 IO25 15 IO26 16 IO27 17 IO14 18 IO12 19 IO13 20 IO15 21 IO2 22 IO0 23 IO4 24 NC_2 25 IO20 26 IO7 27 IO8 28 IO5 29 RXD0 30; TXD0; 35 GND_6; 36 GND_7; 37 GND_8; 38 GND_9; 39 GND_10; 40 GND_11; 41 GND_12; 42 GND_13; 43 GND_14; 44 GND_15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

ESP32-PICO-MINI-02 Bluetooth Module

Title: Bluetooth Module
Author(s): Ryuichi Lin

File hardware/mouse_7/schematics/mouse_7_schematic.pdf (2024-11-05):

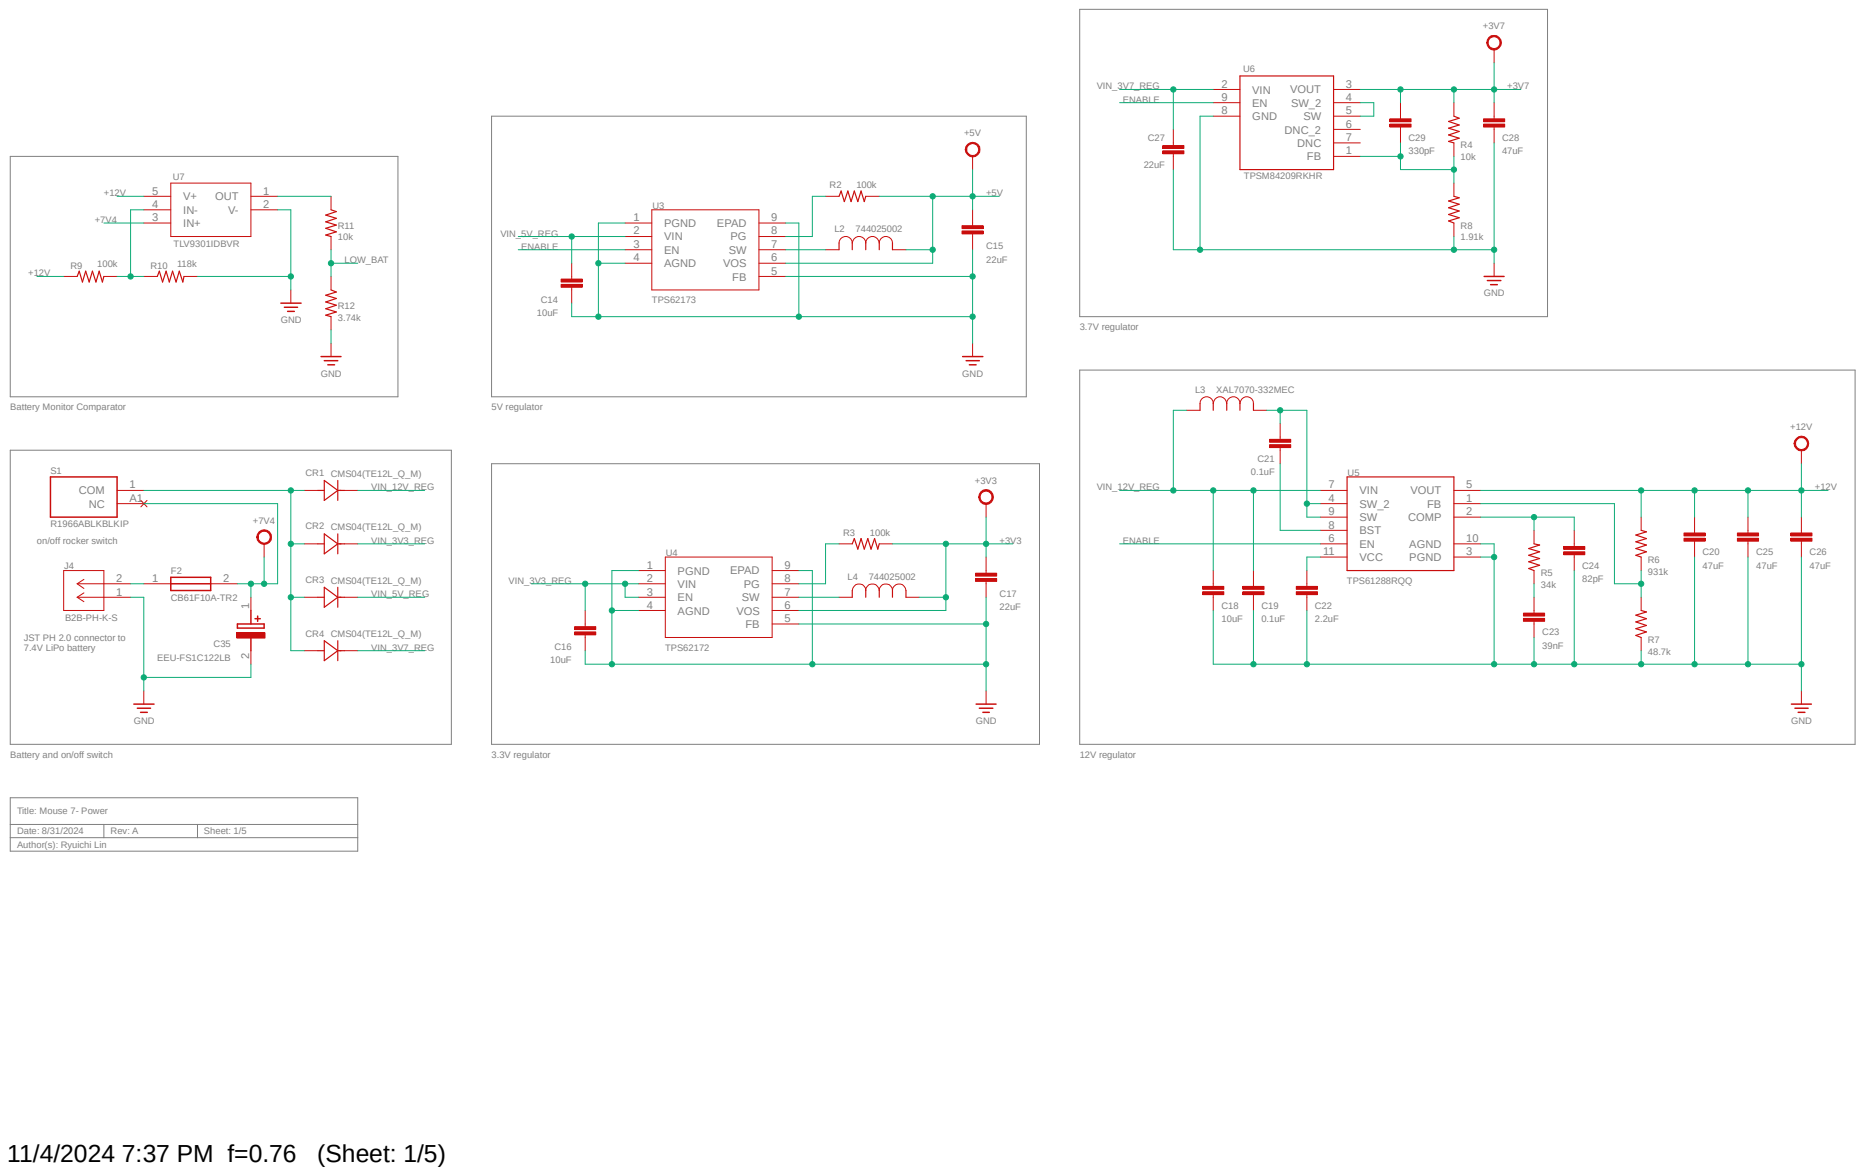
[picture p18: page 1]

3.7V regulator Battery Monitor Comparator B2B-PH-K-S

on/off rocker switch

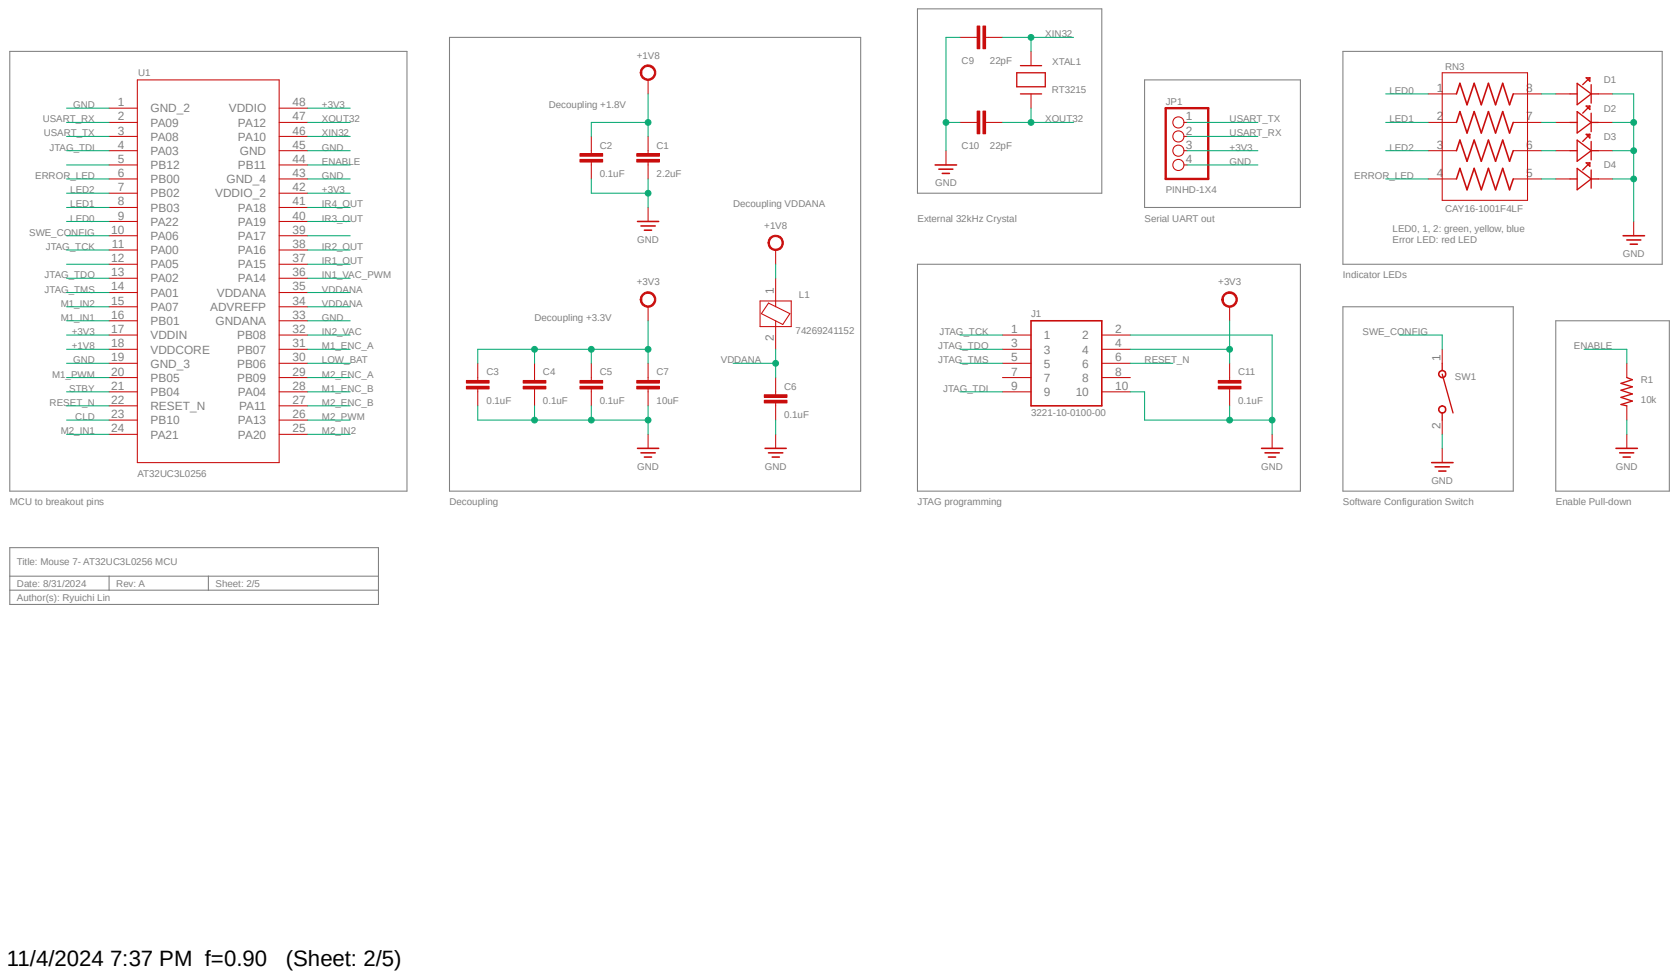
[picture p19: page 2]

Indicator LEDs LED0, 1, 2: green, yellow, blue Error LED: red LED

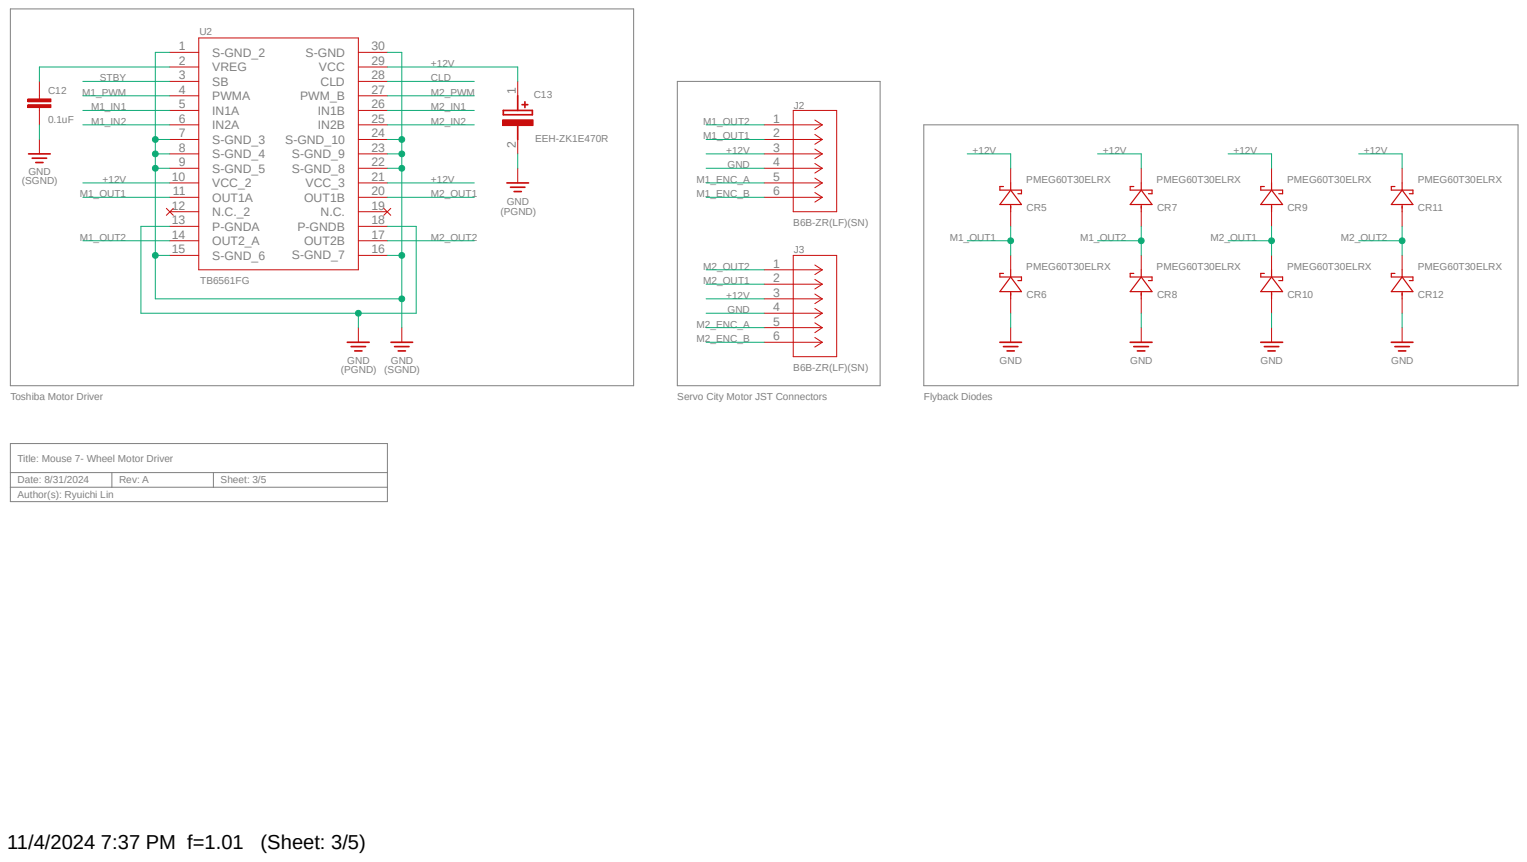
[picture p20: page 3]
11/4/2024 7:37 PM f=1.01 (Sheet: 3/5); (PGND); (SGND); (SGND) Toshiba Motor Driver; Servo City Motor JST Connectors Date: 8/31/2024; Rev: A; Title: Mouse 7- Wheel Motor Driver; Sheet: 3/5 Author(s): Ryuichi Lin; Flyback Diodes TB6561FG; GND GND; GND; PMEG60T30ELRX; PMEG60T30ELRX GND; EEH-ZK1E470R; U2S-GND_2 1; VREG 2; PWMA 4; S-GND_3 7; S-GND_4 8; S-GND_5 9; VCC_2 10; OUT1A 11; P-GNDA 13; OUT2_A 14; S-GND_6 15; S-GND_7; 16 OUT2B; 17 P-GNDB; 19 OUT1B; 20 VCC_3; 21 S-GND_8; 22 S-GND_9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

RN2
1

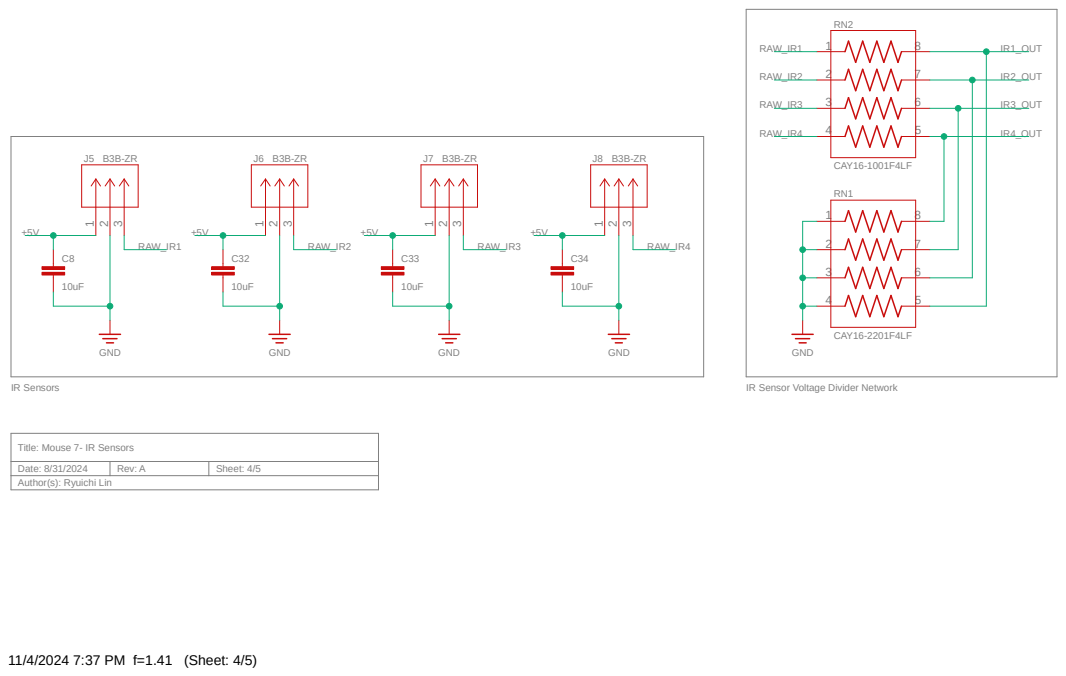
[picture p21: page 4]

Title: Mouse 7- IR Sensors

# OUT1

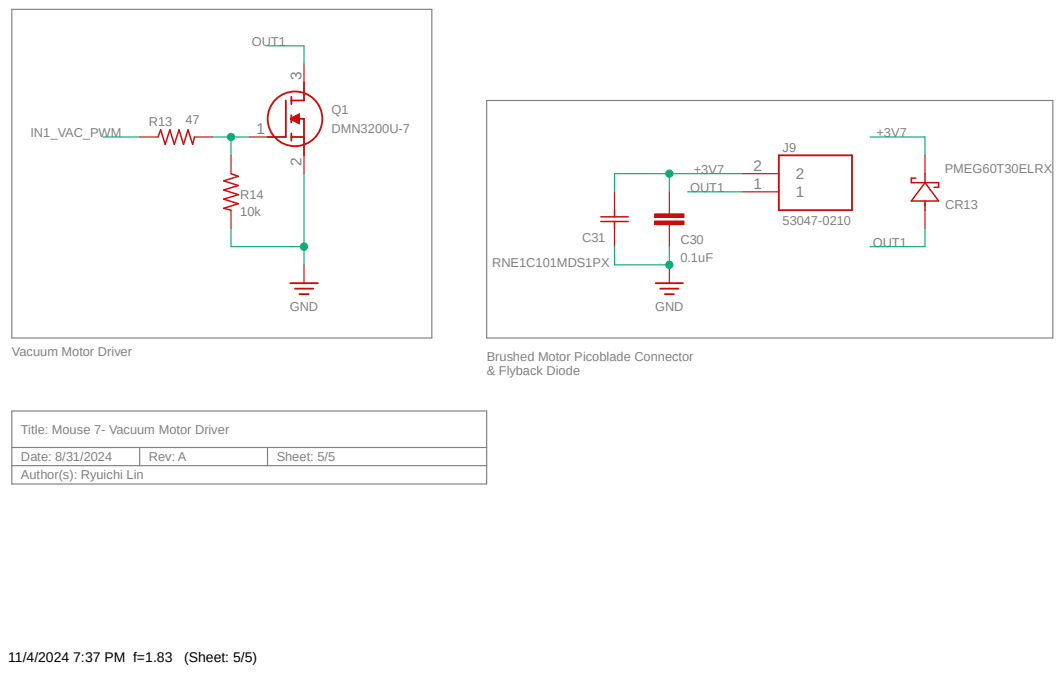
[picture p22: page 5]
11/4/2024 7:37 PM f=1.83 (Sheet: 5/5); Vacuum Motor Driver; Brushed Motor Picoblade Connector; & Flyback Diode; Date: 8/31/2024; Rev: A; Sheet: 5/5; 0.1uF RNE1C101MDS1PX; PMEG60T30ELRX; DMN3200U-7; GND; OUT1; IN1_VAC_PWM

Title: Mouse 7- Vacuum Motor Driver
Author(s): Ryuichi Lin

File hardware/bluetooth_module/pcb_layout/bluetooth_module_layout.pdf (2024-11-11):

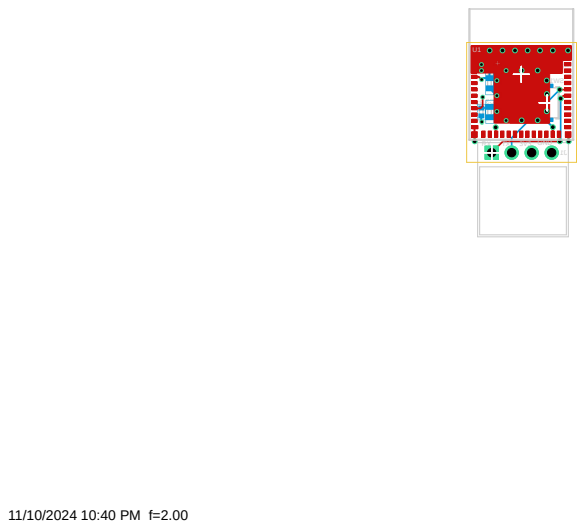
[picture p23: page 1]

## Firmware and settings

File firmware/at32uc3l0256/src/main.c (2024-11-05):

/*-------------------------------- FILE INFO -----------------------------------
* Filename        : main.c
* Author          : Team Kirbo
* Revision        : 1.0
* Updated         : 2024-04-07
* Purpose         : main layer
*
* This is the highest firmware layer containing the main source code to run 
* the micromouse.
*-----------------------------------------------------------------------------*/

/*----------------------------------------------------------------------------*/
/*                               Include Files                                */
/*----------------------------------------------------------------------------*/
#include <stdint.h>
#include <stdlib.h>
#include <stdio.h>
#include "mouse_hardware_interface/leds_mhi.h"
#include "mouse_hardware_interface/power_mhi.h"

#include "mouse_control_interface/init_mci.h"
#include "mouse_control_interface/walldetection_mci.h"
#include "mouse_control_interface/movement_mci.h"
#include "mouse_control_interface/configswitch_mci.h"
#include "mouse_control_interface/time_mci.h"

#include "algo/algo.h"
#include "algo/wallfollower_algo.h"

/*----------------------------------------------------------------------------*/
/*                                Definitions                                 */
/*----------------------------------------------------------------------------*/
/* None */

/*----------------------------------------------------------------------------*/
/*                               Debug Switches                               */
/*----------------------------------------------------------------------------*/
#define DEBUG_MAIN_ENABLE    (0)    /* 1 = Enable Debug Trace Output */

/*----------------------------------------------------------------------------*/
/*                              Global Variables                              */
/*----------------------------------------------------------------------------*/
/* None */

/*----------------------------------------------------------------------------*/
/*                    Private (Static) Function Prototype                     */
/*----------------------------------------------------------------------------*/
/* None */

/*----------------------------------------------------------------------------*/
/*                       Public (Exportable) Functions                        */
/*----------------------------------------------------------------------------*/
/* None */

/*----------------------------------------------------------------------------*/
/*                           Local Shared Functions                           */
/*----------------------------------------------------------------------------*/
/* None */

/*----------------------------------------------------------------------------*/
/*                         Private (Static) Functions                         */
/*----------------------------------------------------------------------------*/

/*----------------------------------------------------------------------------*/
/*                                    Main                                    */
/*----------------------------------------------------------------------------*/
int main (void)
{   
    /* initialize mouse */
    mci_InitializeMouse();
        
    /* infinite while loop */
	
	mhi_DelayMs(2000);
	mci_MoveForwardNSquares(4);
// 	mci_MoveForwardHalfMazeSquarePid();
// 	mhi_DelayMs(2000);

/* 	mci_MoveForwardHalfMazeSquarePid();*/
// 	mci_MoveForward1MazeSquarePid();
// 	mhi_DelayMs(1000);
// 	mci_MoveForwardHalfMazeSquarePid();
// 	mhi_DelayMs(1000);
// 	mci_TurnRight45Degrees();
// 	mhi_DelayMs(1000);
// 	mci_MoveForwardHalfMazeSquarePid();
// 	mhi_DelayMs(1000);
// 	mci_TurnRight90Degrees();
// 	mhi_DelayMs(1000);
// 	mci_MoveForwardHalfMazeSquarePid();
// 	mhi_DelayMs(1000);
// 	mci_MoveForwardHalfMazeSquarePid();
// 	mhi_DelayMs(1000);
// 	mci_TurnLeft90Degrees();
// 	mhi_DelayMs(1000);
// 	mci_MoveForwardHalfMazeSquarePid();
// 	mhi_DelayMs(1000);
// 	mci_MoveForwardHalfMazeSquarePid();
// 	mhi_DelayMs(1000);
// 	mci_TurnRight90Degrees();
// 	mhi_DelayMs(1000);
// 	mci_MoveForwardHalfMazeSquarePid();
// 	mhi_DelayMs(1000);
// 	mci_TurnRight45Degrees();
// 	mhi_DelayMs(1000);
// 	mci_MoveForwardHalfMazeSquarePid();
//     while(1)
//     {
//         mhi_CheckLowBattery();
//         
// 		traverseCell();
// // 		if(mci_CheckFrontWall()){
// // 			mci_AdjustToFrontWall();
// // 		}
// 		
//     }
}

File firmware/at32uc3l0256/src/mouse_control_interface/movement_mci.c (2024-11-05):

/*-------------------------------- FILE INFO -----------------------------------
* Filename        : movement_mci.c
* Author          : Team Kirbo
* Revision        : 1.0
* Updated         : 2024-04-13
* Purpose         : mouses control interface layer
*
* This is the header file for mouse movement under the mouse control
* interface.
*
* The mouse control interface uses the mouse hardware interface to define high
* level micromouse functionality.
*-----------------------------------------------------------------------------*/

/*----------------------------------------------------------------------------*/
/*                               Include Files                                */
/*----------------------------------------------------------------------------*/
#include <stdint.h>
#include <stdio.h>
#include <stdlib.h>
#include <math.h>
#include "micromouse_dimensions.h"
#include "shared_functions/constrain_sf.h"
#include "mouse_hardware_interface/leds_mhi.h"
#include "mouse_hardware_interface/usart_mhi.h"
#include "mouse_hardware_interface/irsensors_mhi.h"
#include "mouse_control_interface/walldetection_mci.h"
#include "mouse_hardware_interface/motors_mhi.h"
#include "mouse_hardware_interface/interrupts_mhi.h"
#include "mouse_control_interface/movement_mci.h"
#include "mouse_control_interface/walldetection_mci.h"

/*----------------------------------------------------------------------------*/
/*                                Definitions                                 */
/*----------------------------------------------------------------------------*/
/* None */

/*----------------------------------------------------------------------------*/
/*                               Debug Switches                               */
/*----------------------------------------------------------------------------*/
/* 1 = Enable Debug Trace Output */
#define DEBUG_MCI_MOVEMENT_ENABLE    (1)

/*----------------------------------------------------------------------------*/
/*                              Global Variables                              */
/*----------------------------------------------------------------------------*/
/* None */

/*----------------------------------------------------------------------------*/
/*                    Private (Static) Function Prototype                     */
/*----------------------------------------------------------------------------*/
/* None */

/*----------------------------------------------------------------------------*/
/*                       Public (Exportable) Functions                        */
/*----------------------------------------------------------------------------*/
/**
* Move mouse 1 wheel revolution
*
* Made for debugging purposes
*
* \param None
* \retval None
*/
void mci_MoveForward1Revolution(void)
{
    uint32_t rightDone = 0u;
    uint32_t leftDone = 0u;
    
    /* reset encoder counts */
    mhi_ClearEncoder1EdgeCount();
    mhi_ClearEncoder2EdgeCount();
    
    /* set speed and start in forward direction */
    mhi_SetWheelMotor1Speed(MCI_MINIMUM_SPEED);
    mhi_StartWheelMotor1Forward();
    mhi_SetWheelMotor2Speed(MCI_MINIMUM_SPEED);
    mhi_StartWheelMotor2Forward();
    
    /* keep moving motors until encoder edge counts are reached */
    while((!rightDone) || (!leftDone))
    {
        /* right motor */
        if ((!rightDone) && (mhi_GetEncoder1EdgeCount() >= MCI_WHEEL_MOTOR_EDGES_PER_REVOLUTION))
        {
            mhi_StopWheelMotor1();
            rightDone = 1u;
            mhi_PrintString("stopped motor 1: ");
            mhi_PrintInt(mhi_GetEncoder1EdgeCount());
            mhi_PrintString("\r\n");
        }
        else if (mhi_GetEncoder1EdgeCount() >= (MCI_WHEEL_MOTOR_EDGES_PER_REVOLUTION / 3))
        {
            mhi_SetWheelMotor1Speed(MCI_FORWARD_FAST_SPEED);
        }
        else if (mhi_GetEncoder1EdgeCount() >= ((MCI_WHEEL_MOTOR_EDGES_PER_REVOLUTION / 3) * 2))
        {
            mhi_SetWheelMotor1Speed(MCI_MINIMUM_SPEED);
        }
        
        /* left motor */
        if ((!leftDone) && (mhi_GetEncoder2EdgeCount() >= MCI_WHEEL_MOTOR_EDGES_PER_REVOLUTION))
        {
            mhi_StopWheelMotor2();
            leftDone = 1u;
            mhi_PrintString("stopped motor 2: ");
            mhi_PrintInt(mhi_GetEncoder2EdgeCount());
            mhi_PrintString("\r\n");
        }
        else if (mhi_GetEncoder2EdgeCount() >= (MCI_WHEEL_MOTOR_EDGES_PER_REVOLUTION / 3))
        {
            mhi_SetWheelMotor2Speed(MCI_FORWARD_FAST_SPEED);
        }
        else if (mhi_GetEncoder2EdgeCount() >= ((MCI_WHEEL_MOTOR_EDGES_PER_REVOLUTION / 3) * 2))
        {
            mhi_SetWheelMotor2Speed(MCI_MINIMUM_SPEED);
        }
    }
    
    mhi_PrintString("final: ");
    mhi_PrintInt(mhi_GetEncoder1EdgeCount());
    mhi_PrintString(" ");
    mhi_PrintInt(mhi_GetEncoder2EdgeCount());
    mhi_PrintString("\r\n");
    
    /* clear encoder edge counts and set motor speeds to 0 */
    mhi_ClearEncoder1EdgeCount();
    mhi_ClearEncoder2EdgeCount();
    mhi_SetWheelMotor1Speed(0);
    mhi_SetWheelMotor2Speed(0);
}
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

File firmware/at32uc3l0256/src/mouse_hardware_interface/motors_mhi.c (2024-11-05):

/*-------------------------------- FILE INFO -----------------------------------
* Filename        : motors_mhi.c
* Author          : Team Kirbo
* Revision        : 1.0
* Updated         : 2024-04-07
* Purpose         : mouse hardware interface layer
*
* This is the source file for the mouse motors interface.
* This includes brushed DC vacuum and wheel motor control interfaces.
*
* The mouse hardware interface uses the HAL to define functions needed to
* interface w/ all mouse hardware.
*
* TODO:
*     - Add contracts and handlers for this MHI layer as well
*     - Check and handle status return values of IO HAL functions
*
* (if applicable)
* Target Hardware    : AT32UC3L0256
* IDE                : Atmel Studio 7.4.2542
* SDK                : ASF 3.52.0
*-----------------------------------------------------------------------------*/

/*----------------------------------------------------------------------------*/
/*                               Include Files                                */
/*----------------------------------------------------------------------------*/
#include <asf.h> //embodiment of pain- defeats abstraction effort
#include <stdint.h>
#include <stdio.h>
#include "HAL/HAL_contracts/io_contract.h"
#include "HAL/HAL_configs/io_config.h"
#include "leds_mhi.h"
#include "HAL/HAL_contracts/pwm_contract.h"
#include "HAL/HAL_configs/pwm_config.h"
#include "motors_mhi.h"

/*----------------------------------------------------------------------------*/
/*                                Definitions                                 */
/*----------------------------------------------------------------------------*/
/* None */

/*----------------------------------------------------------------------------*/
/*                               Debug Switches                               */
/*----------------------------------------------------------------------------*/
/* None */

/*----------------------------------------------------------------------------*/
/*                              Global Variables                              */
/*----------------------------------------------------------------------------*/
static mhi_wheel_motor_direction_t wheelMotor1Direction 
    = MHI_WHEEL_MOTOR_DIRECTION_STOP;

static mhi_wheel_motor_direction_t wheelMotor2Direction
    = MHI_WHEEL_MOTOR_DIRECTION_STOP;

static mhi_vacuum_motor_state_t vacuumMotorState
    = MHI_VACUUM_MOTOR_STATE_STOP;
/*----------------------------------------------------------------------------*/
/*                    Private (Static) Function Prototype                     */
/*----------------------------------------------------------------------------*/
/* None */

/*----------------------------------------------------------------------------*/
/*                       Public (Exportable) Functions                        */
/*----------------------------------------------------------------------------*/
/**
* Initialize PWM interface for micromouse.
*
* \param  None
* \retval None
*/
void mhi_InitPwm(void)
{
    pwm_handler_t *pwmInterface = NULL;
    config_GetPwmHandler(&pwmInterface);
    
    if (pwmInterface->pwm_Init() != PWM_SUCCESS)
        mhi_IndicateError(MHI_LEDS_PWM_ERROR);
}

/**
* Initialize wheel motor control pins for micromouse.
*
* \param  None
* \retval None
*/
void mhi_InitWheelMotors(void)
{
    io_handler_t *ioInterface = NULL;
    config_GetIOHandler(&ioInterface);
    
    ioInterface->io_Init(0u, MHI_WHEEL_MOTOR_STANDBY_PIN, 
        IO_PIN_LOW, IO_OUTPUT, IO_PULLUP_DISABLE);
        
    ioInterface->io_Init(0u, MHI_WHEEL_MOTOR_CLD_PIN,
        IO_PIN_LOW, IO_INPUT, IO_PULLUP_DISABLE);
    
    ioInterface->io_Init(0u, MHI_WHEEL_MOTOR_1_IN1_PIN,
        IO_PIN_LOW, IO_OUTPUT, IO_PULLUP_DISABLE);
    
    ioInterface->io_Init(0u, MHI_WHEEL_MOTOR_1_IN2_PIN,
        IO_PIN_LOW, IO_OUTPUT, IO_PULLUP_DISABLE);
    
    ioInterface->io_Init(0u, MHI_WHEEL_MOTOR_2_IN1_PIN,
        IO_PIN_LOW, IO_OUTPUT, IO_PULLUP_DISABLE);
    
    ioInterface->io_Init(0u, MHI_WHEEL_MOTOR_2_IN2_PIN,
        IO_PIN_LOW, IO_OUTPUT, IO_PULLUP_DISABLE);
}

/**
* Initialize vacuum motor control pins for micromouse.
*
* \param  None
* \retval None
*/
void mhi_InitVacuumMotor(void)
{
    io_handler_t *ioInterface = NULL;
    config_GetIOHandler(&ioInterface);
    
    ioInterface->io_Init(0u, MHI_VACUUM_MOTOR_IN1_PIN,
        IO_PIN_LOW, IO_OUTPUT, IO_PULLUP_DISABLE);
}

/**
* Start micromouse wheel motor 1 in forward direction.
*
* \param  None
* \retval None
*/
void mhi_StartWheelMotor1Forward(void)
{
    io_handler_t *ioInterface = NULL;
    config_GetIOHandler(&ioInterface);
    
    wheelMotor1Direction = MHI_WHEEL_MOTOR_DIRECTION_FORWARD;
    ioInterface->io_WriteOutput(0u, MHI_WHEEL_MOTOR_STANDBY_PIN, IO_PIN_HIGH);
    ioInterface->io_WriteOutput(0u, MHI_WHEEL_MOTOR_1_IN1_PIN, IO_PIN_HIGH);
    ioInterface->io_WriteOutput(0u, MHI_WHEEL_MOTOR_1_IN2_PIN, IO_PIN_LOW);
}

/**
* Start micromouse wheel motor 1 in backward direction.
*
* \param  None
* \retval None
*/
void mhi_StartWheelMotor1Backward(void)
{
    io_handler_t *ioInterface = NULL;
    config_GetIOHandler(&ioInterface);
    
    wheelMotor1Direction = MHI_WHEEL_MOTOR_DIRECTION_BACKWARD;
    ioInterface->io_WriteOutput(0u, MHI_WHEEL_MOTOR_STANDBY_PIN, IO_PIN_HIGH);
    ioInterface->io_WriteOutput(0u, MHI_WHEEL_MOTOR_1_IN1_PIN, IO_PIN_LOW);
    ioInterface->io_WriteOutput(0u, MHI_WHEEL_MOTOR_1_IN2_PIN, IO_PIN_HIGH);
}

/**
* Set micromouse wheel motor 1 duty cycle.
*
* \param[in] speed Duty cycle to set wheel motor 1 to (0~255)
* \retval None
*/
void mhi_SetWheelMotor1Speed(uint16_t speed)
{
    pwm_handler_t *pwmInterface = NULL;
    config_GetPwmHandler(&pwmInterface);
    
    if (pwmInterface->pwm_SetWheelMotor1DutyCycle(speed) != PWM_SUCCESS)
        mhi_IndicateError(MHI_LEDS_PWM_ERROR);
}

/**
* Stop micromouse wheel motor 1.
*
* \param  None
* \retval None
*/
void mhi_StopWheelMotor1(void)
{
    io_handler_t *ioInterface = NULL;
    config_GetIOHandler(&ioInterface);
    
    mhi_SetWheelMotor1Speed(0u);
    wheelMotor1Direction = MHI_WHEEL_MOTOR_DIRECTION_STOP;
    ioInterface->io_WriteOutput(0u, MHI_WHEEL_MOTOR_STANDBY_PIN, IO_PIN_HIGH);
    ioInterface->io_WriteOutput(0u, MHI_WHEEL_MOTOR_1_IN1_PIN, IO_PIN_HIGH);
    ioInterface->io_WriteOutput(0u, MHI_WHEEL_MOTOR_1_IN2_PIN, IO_PIN_HIGH);
}

/**
* Access function for wheel motor 1 direction
*
* \param  None
* \retval wheelMotor1Direction Direction variable for wheel motor 1
*/
mhi_wheel_motor_direction_t mhi_GetWheelMotor1Direction(void)
{
    return wheelMotor1Direction;
}
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

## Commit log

2024-11-05 docs: add hardware reference files
    [Battery Mount- 450mAh LiPo v5.3mf, sharp sensor mount 2.0 v7.3mf, vacuum fan 7 v2.3mf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]
2024-11-11 docs: add mouse 7 bill of materials
